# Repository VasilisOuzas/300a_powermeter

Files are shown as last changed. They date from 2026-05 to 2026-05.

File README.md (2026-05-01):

# 300a Powermeter
This project was created, so that we could exceed our currrent meter limitation for the orange cube + by creating our own hall effect based current meter board.
### General Inforamtion:
The ardupilot cube orange+ unit comes out of the box with a 30A max current meter. 
We wanted to use the orange plus for our UAV drone, aiming to compete at the 2026 [UAS challenge](https://www.imeche.org/events/challenges/uas-challenge) as members of [Starbound Team](https://starbound.e-ce.uth.gr/).

Our main challenge was the need for a current meter that can measure Amperage of at least 250A. The current meter included with the orange plus is limited to 30A maximum.
We designed a custom PCB responsible for current sensing of at least 250A. For our purposes, we chose the ACS772 (250-CS772ECB300BPFFT) hall effect sensor. 
For more information please check the [Starbound_Power_Meter_Design.pdf](https://github.com/VasilisOuzas/300a_powermeter/blob/main/Starbound__Power_Meter_Design.pdf)

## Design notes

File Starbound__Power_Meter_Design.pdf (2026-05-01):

## Power Meter Analysis & Design

Sokratis Soutsiou
Ouzas Vasileios

March 24, 2026

Introduction

The scope of this report is to analyze the existing power meter included with the Orange Cube Plus and to design a new one from scratch, rated for a total current of at least 250A compared to the 30A maximum rating of the provided module.

Analysis of the included module

No documentation is available, so the PCB was inspected under a microscope to understand how the module operates and communicates with the Cube Orange+.

Three main components can be identified immediately on the PCB:

- A 25 mΩ resistor used as a current shunt. The voltage across the shunt follows Ohm’s law:
V = IR

At 30 A:
V = 30 × 0.025 = 0.75 V

The power dissipated is:

P = I

2R = 30² × 0.025 = 22.5W

At 250 A:

V = 250 × 0.025 = 6.25 V, P = 250² × 0.025 = 1562.5W ≈ 1.56 kW

This would waste significant power and require substantial cooling. A Hall-effect current sensor is preferable, as it adds negligible resistance and dissipates far less power.

- LT8610: An LT8610 Synchronous Buck Converter to efficiently step down the high LiPo battery voltage to a stable and accurate 5 V (fixed version) to power the Cube Orange+ and onboard electronics.
- INA169: The INA169 measures the small voltage (0.75V) across the shunt and directly converts it into an output signal using an external resistor that sets the gain. This allows the output voltage to be scaled as needed to 0–3.3 V for the ADC.

- An SMD chip marked 8VHAB - no datasheet found, but probably is an OpAmp Buffer Stage for the ADC signal.

The board connects to the Cube Orange+ through a cable to POWER1. Based on [link], it is found that the cable uses a JST-GH 1.25 mm 6-pin connector at the power meter end (same type used for other com ports) and a Molex CLIK-Mate 2.0 mm 6-pin connector at the Cube Orange+ POWER1 end. The pinout of POWER1 is as follows:

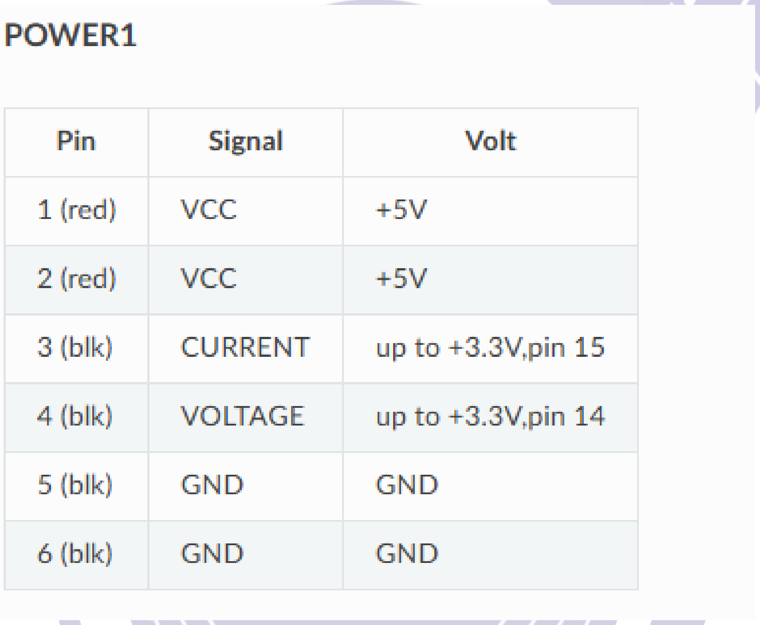
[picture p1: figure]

Figure 1: POWER1 Port Pinout

both current and voltage sense pins are analog voltages with a range of 0-3.3V.

Design of New Power Meter

Current Meter Choice

The ACS772 (250-CS772ECB300BPFFT) is chosen because it can pass up to 300A, handles calibration internally and outputs an analog voltage which the cube orange + ADC can read.

- Decoupling capacitor (Cp): 100 nF mlcc recommended by the datasheet.
- Low-pass filter (Rf–Cf): Chosen to capture fast motor current transients while filtering high-frequency noise:

Rf = 1 kΩ, | Cf = 10 nF | ⇒ | fc =

1
2πRfCf

≈ 15.9 kHz

T =

1
fc

≈ 63 µs, which is sufficient to capture signal spikes.

Current Meter Output Translation

According to the datasheet of the ACS772 (250-CS772ECB300BPFFT), the sensor output is ratiometric around a mid-supply reference. When powered from VCC:

- Zero-current output: approximately VCC/2
- Sensitivity (300 A version): approximately 6.66 mV × VCC/5 per A

The output voltage of the sensor is therefore

VACS =

VCC
2

+

6.66 mV ·

VCC

5 V
- I

For VCC = 5 V and the 300 A measurement range:

I = 0 A ⇒ VACS ≈ 2.5 V

I = 300 A ⇒ VACS ≈ 2.5 + 300 · 6.66 mV ≈ 4.498 V

Thus the useful output range of the sensor is approximately

2.5 V ≤ VACS ≤ 4.498 V

The CubePilot Orange ADC input range is 0–3.3 V, therefore for maximum accuracy the voltage signal must be translated and scaled to this range. Since only positive current is measured, the first step is removing the 2.5 V offset:

0 V ≤ V curr ≤ 1.998 V

To utilize the full ADC input range, the signal is then amplified so that 0–1.998 V maps to 0–3.3 V. The required gain is

G =

3.3
1.998

≈

3.3
2

= 1.65

The final voltage applied to the ADC is therefore

0 V ≤ V curr ≤ 3.2967 V

This translation can be implemented using an operational amplifier configured as a differential amplifier with gain, using standard resistor values R1 = 2 kΩ and R2 = 3.3 kΩ or with multiturn potentiometers in place of R2 for fine tuning. Also any voltage offset can be calibrated through software.

Voltage Meter

For the voltage meter, a simple resistor divider can be used since there is no need for big accuracy (in the decimal range) for the voltage. To scale down the full 6S battery voltage (25.2 V) to the ADC range (0–3.3 V), a division factor of approximately 7.64 is required. Choosing the bottom resistor as 10 kΩ and the top resistor as 68 kΩ gives:

Vout = Vin ·

Rbottom

Rtop + Rbottom

= 25.2 ·

10
68 + 10

≈ 3.2308 V

at maximum battery voltage, which is safely within the ADC limit.

As a result, the usable measurement range for battery voltage is reduced to a window of approximately 0.69 V (2.54 V to 3.23 V). While this represents a loss of theoretical precision, the 12-bit ADC of the Cube Orange+ still provides a resolution of approximately 6.2 mV per bit at the battery level, which is more than sufficient for flight telemetry. The specific voltage and current multipliers can be calibrated within the ArduPilot.

5V LDO Regulator

Since a stable, low noise and low current 5V supply is needed, a linear LDO regulator is chosen. The estimated current draw from the 5 V rail (excluding the LDO’s own quiescent current) is calculated as follows:

- ACS772 Sensor: According to the datasheet, the typical operating current is 10 mA, with a maximum of 15 mA.
- MCP6002T Op-Amp: This dual rail-to-rail op-amp has a maximum quiescent current of 170 µA per amplifier. For both channels, the total draw is approximately 0.34 mA.
- VCC Halfer (VCC/2): A 10 kΩ/10 kΩ divider is used to create the 2.5 V reference for the differential stage. The current through this branch is:

Idiv =

5 V
10 kΩ + 10 kΩ = 0.25 mA
- Differential Amp - Reference Path: The non-inverting input of the op-amp is connected to a divider. For R1 = 2 kΩ and R2 = 3.3 kΩ connected to the 2.5 V reference:

Ipath1 =

2.5 V
R1 + R2

=

2.5 V
5.3 kΩ

≈ 0.47 mA

- Differential Amp - Feedback Path: The current through the feedback loop from the output to the inverting input. At max scale (Vout = 3.3 V):

Ipath2 ≈

Vout − Vin−
R2

≈

3.3 V − 2.5 V
3.3 kΩ

≈ 0.24 mA

- Status LED: Using a 1 kΩ current-limiting resistor for a red SMD LED (Vf ≈ 2 V), the current is:

ILED =

5 V − 2 V
1000 Ω = 3 mA
- Total Estimated Current (Itotal): Summing these maximums, the circuit requires approximately 19.30 mA.

While the current is relatively low, the power dissipation (PD) across the LDO at a maximum 6S battery voltage of 25.2 V is the primary design constraint:

PD = (Vin − Vout) · Itotal = (25.2 V − 5 V) · 0.0193 A ≈ 0.39W

This remains well within the thermal limits of a SOT-223 package, which typically handles up to 0.5W - 1W.

References

- Allegro MicroSystems ACS772 Current Sensor: https://gr.mouser.com/ProductDetail/

Allegro-MicroSystems/ACS772ECB-300B-PFF-T?qs=HoCaDK9Nz5e9MqYr4%2BWi3Q%3D%3D (https://gr.mouser.com/ProductDetail/Allegro-MicroSystems/ACS772ECB-300B-PFF-T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)

- PCB Headers (RS Online): https://uk.rs-online.com/web/p/pcb-headers/5468827
- CubePilot Interface Specifications: https://docs.cubepilot.org/user-guides/autopilot/

the-cube/introduction/interface-specifications (https://docs.cubepilot.org/user-guides/autopilot/the-cube/introduction/interface-specifications)

- Connector Datasheet (Distrelec): https://media.distrelec.com/Web/Downloads/_t/ds/

HX4-06008_eng_tds.pdf (https://media.distrelec.com/Web/Downloads/_t/ds/HX4-06008_eng_tds.pdf)

- ArduPilot Mauch Power Modules Documentation: https://ardupilot.org/copter/docs/

common-mauch-power-modules.html (https://ardupilot.org/copter/docs/common-mauch-power-modules.html)

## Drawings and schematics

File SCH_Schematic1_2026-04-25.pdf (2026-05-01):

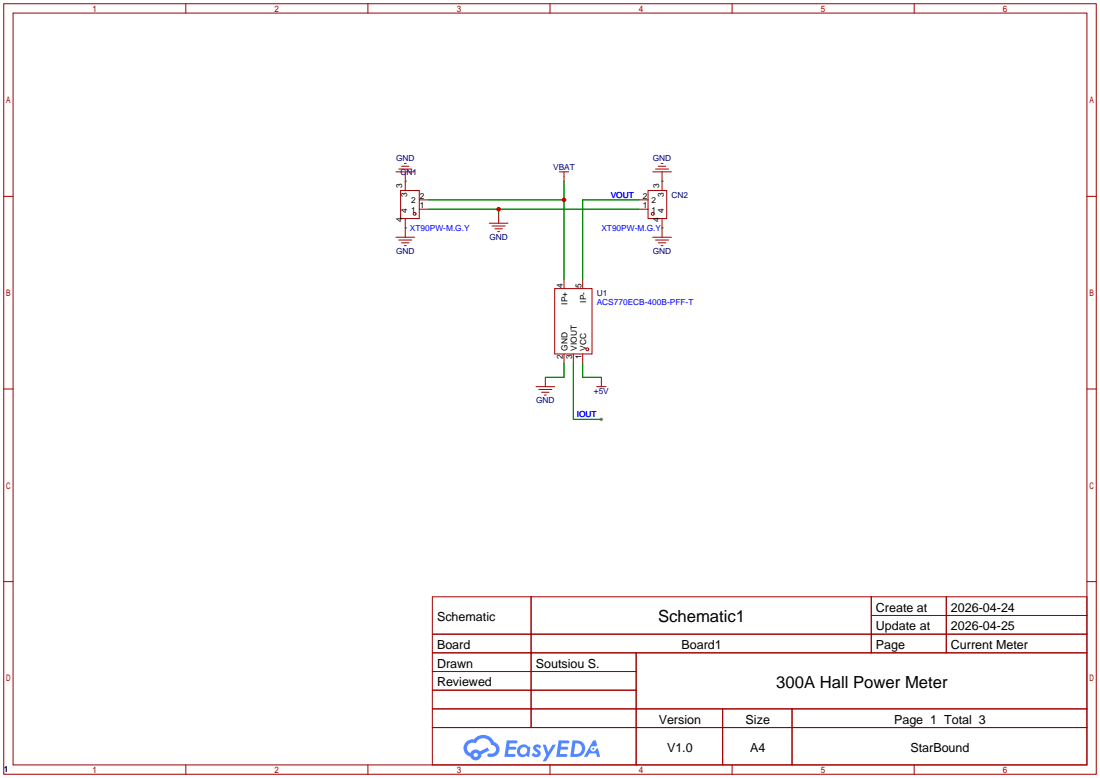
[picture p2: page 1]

Schematic | Schematic1 | Create at | 2026-04-24

Update at | 2026-04-25

Board | Board1 | Page | Current Meter
Drawn | Soutsiou S. | 300A Hall Power Meter
Reviewed

Version | Size | Page 1 Total 3
V1.0 | A4 | StarBound

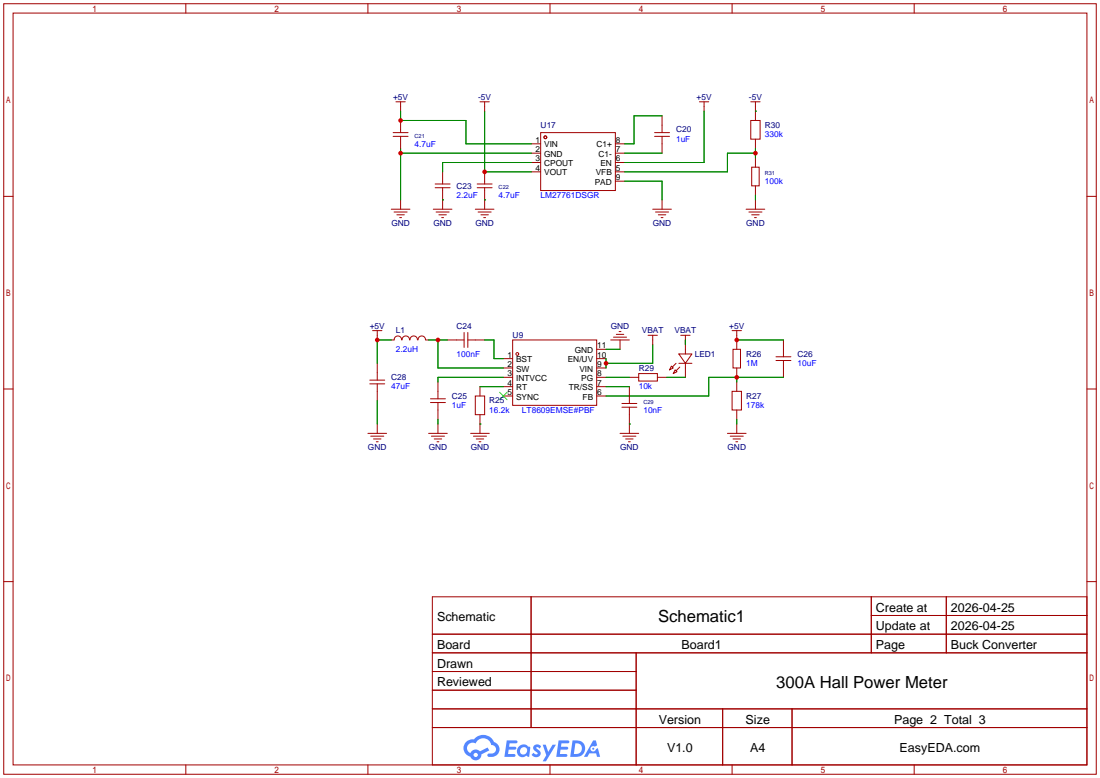
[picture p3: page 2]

Schematic | Schematic1 | Create at | 2026-04-25

Update at | 2026-04-25

Board | Board1 | Page | Buck Converter
Drawn | | 300A Hall Power Meter
Reviewed

Version | Size | Page 2 Total 3
V1.0 | A4 | EasyEDA.com

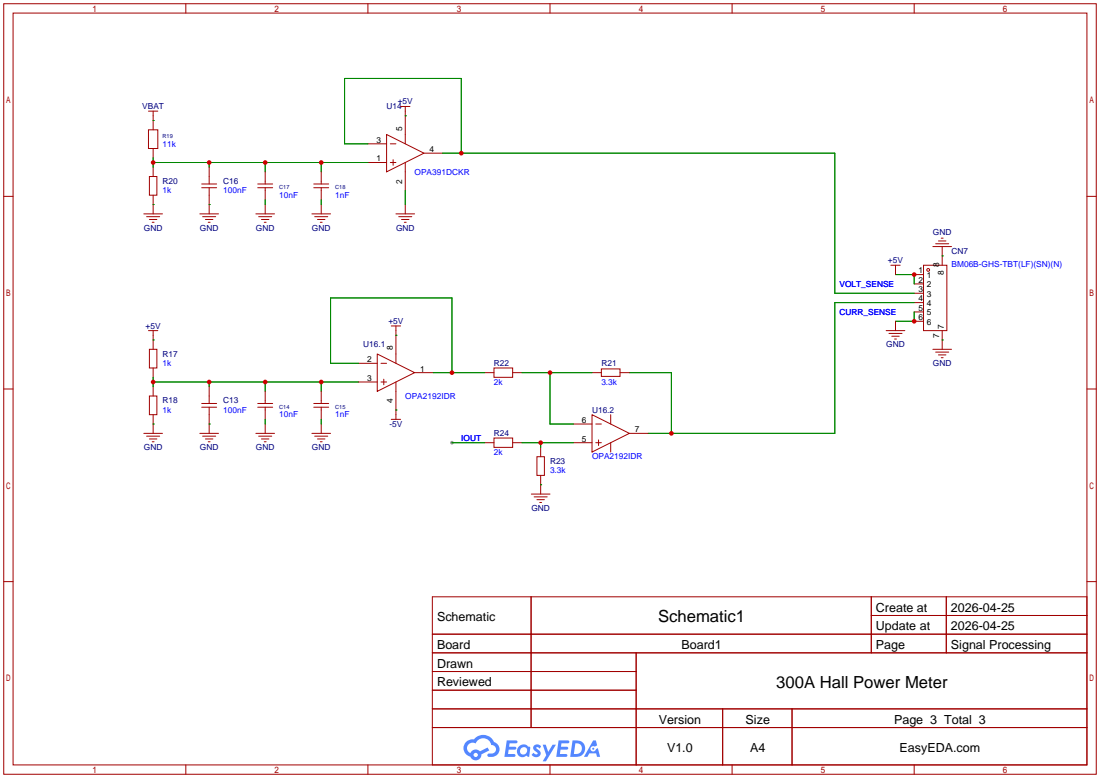
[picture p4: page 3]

Schematic | Schematic1 | Create at | 2026-04-25

Update at | 2026-04-25

Board | Board1 | Page | Signal Processing
Drawn | | 300A Hall Power Meter
Reviewed

Version | Size | Page 3 Total 3
V1.0 | A4 | EasyEDA.com

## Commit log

2026-04-24 First commit of the project
    [current_meter_remaster1.SchDoc]
2026-05-01 added the finilized pcb schematics
